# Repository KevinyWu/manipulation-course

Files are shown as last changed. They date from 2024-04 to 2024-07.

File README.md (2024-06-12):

# Robotic Manipulation Course

- [Robotic Manipulation Course](#robotic-manipulation-course)
  - [Course Setup](#course-setup)
  - [Dynamixel Robot Arm](#dynamixel-robot-arm)
    - [Required Materials](#required-materials)
    - [Assembly](#assembly)

## Course Setup

Clone the repo and create a virtual environment. We use Python 3.10.12.

```bash
# Clone the repository
git clone https://github.com/KevinyWu/manipulation-course.git
cd manipulation-course

# Create a virtual environment in the project root
python3 -m venv env

# Add the project to the PYTHONPATH in the virtual environment
echo 'export PYTHONPATH="$PYTHONPATH:/absolute/path/to/manipulation-course"' >> env/bin/activate

# Activate the virtual environment
source env/bin/activate

# Install the dependencies
pip install -r requirements.txt

# To deactivate the virtual environment
deactivate
```

## Dynamixel Robot Arm

This repository contains the files to build and control a low-cost robot arm that costs about $160. The design is adapted from [low_cost_robot](https://github.com/AlexanderKoch-Koch/low_cost_robot) by [Alexander Koch](https://github.com/AlexanderKoch-Koch).

This robot arm uses Dynamixel XL330 servo motors that weigh only 18g each. This makes the arm very lightweight and fast.
Dynamixel sells the U2D2 adapter to connect the servos to a computer. However, this is very expensive and the latency is very high. This build uses another cheaper adapter board instead.
The robot arm can be controlled with the Dynamixel SDK: ```pip install dynamixel-sdk```

### Required Materials

| Part | Cost | Buying link | Notes |
|---|---|---| --- |
| 5x Dynamixel XL330-M288 | $120  | https://www.robotis.us/dynamixel-xl330-m288-t/ | [Specs](https://emanual.robotis.com/docs/en/dxl/x/xl330-m288/)|
| XL330 Idler Wheel | $10  | https://www.robotis.us/fpx330-h101-4pcs-set/ | Pack of four; only three needed |
| XL330 Frame | $9 | https://www.robotis.us/fpx330-s101-4pcs-set/ | Pack of four; only one needed |
| Waveshare Serial Bus Servo Driver Board | $5  | https://www.waveshare.com/bus-servo-adapter-a.htm | |
| Waveshare OV5693 5MP USB Camera | $30  | https://www.waveshare.com/product/ov5693-5mp-usb-camera-a.htm | |
| 5V Power Supply | $6 | https://a.co/d/5u90NVp | |
| Table Clamp | $6 | https://a.co/d/4KEiYdV | |
| Wires | $7 | https://a.co/d/hQfk2cb | |
| Rubber Sheet | $2 | https://a.co/d/bEoalHQ | |
| USB-C Cable | $8 | https://a.co/d/fA40KHY | Pack of two, only one needed|
| Total | $194 | | |

There is usually a 10% discount code for the Robotis shop.

### Assembly

Video of the assembly: MAKE VIDEO

1. Print all parts with a 3D printer
   1. The STL files are in `hardware/stl`
   2. The parts are designed to be easy to print; only the moving part of the gripper needs supports
2. Scanning motors
   1. Connect the driver board to a computer (should work with Linux and MacOS)
   2. Figure out the device name (e.g. tty.usbmodem57380045631 for MacOS): ```ls /dev/tty.*```
   3. Scan each motor individually with [Dynamixel Wizard](https://emanual.robotis.com/docs/en/software/dynamixel/dynamixel_wizard2/)
      1. (Linux) Allow access to USB ports, then reboot for changes to take effect: `sudo usermod -aG dialout <your_account_id>; reboot`
      2. Set the baudrate to 1M for all motors
      3. Set the servo IDs to 1 for the shoulder to 5 for the gripper servo
3. Assembly
   1. Assemble the arm without the base
      1. Make sure that the servos are fixed in the same position as in the CAD
      2. Ensure the default servo angles are all 180 degrees (when the arm is in the position shown in the image below, all servos should be at 180 degrees as shown on the right image from Dynamixel Wizard)
   2. Screw the servo driver board onto the base
   3. Screw the base onto the arm
   4. Connect D, V, and G ports on the driver board to the shoulder rotation servo
   5. Connect successive servos to each other
   6. Connect the driver board to the power supply

<p align="center">
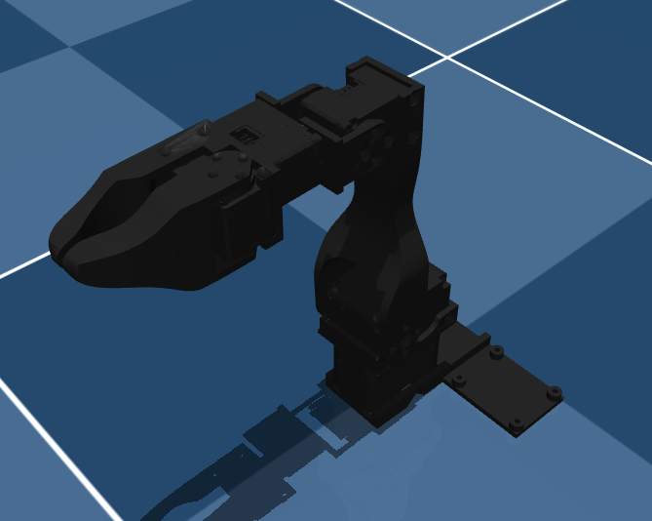
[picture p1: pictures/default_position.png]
default_position
   
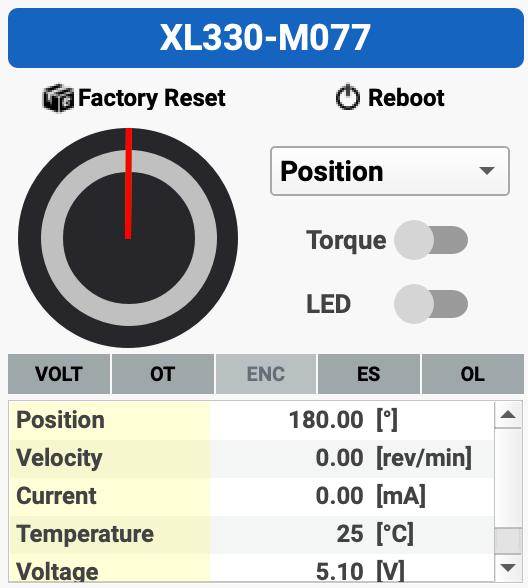
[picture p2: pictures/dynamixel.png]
dynamixel
   
</p>

**Note**: Ensure the default servo angles are all 180 degrees when the arm is in the position shown in the simulation above. Also note that counterclockwise is negative for rotation in Dynamixel Wizard.

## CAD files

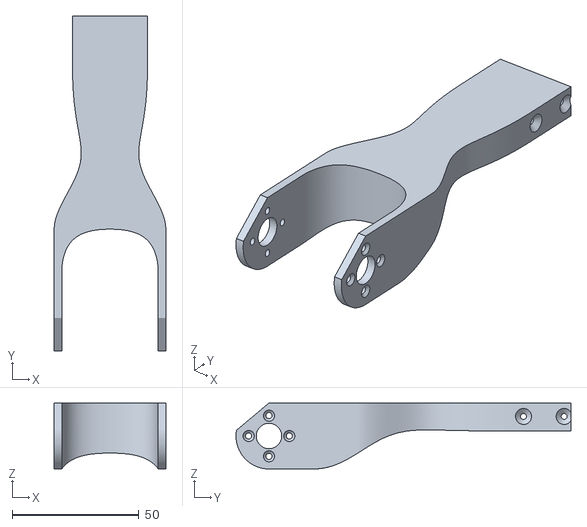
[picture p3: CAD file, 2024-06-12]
hardware/arm/shoulder_to_elbow.stl
44.0 x 132.0 x 26.0

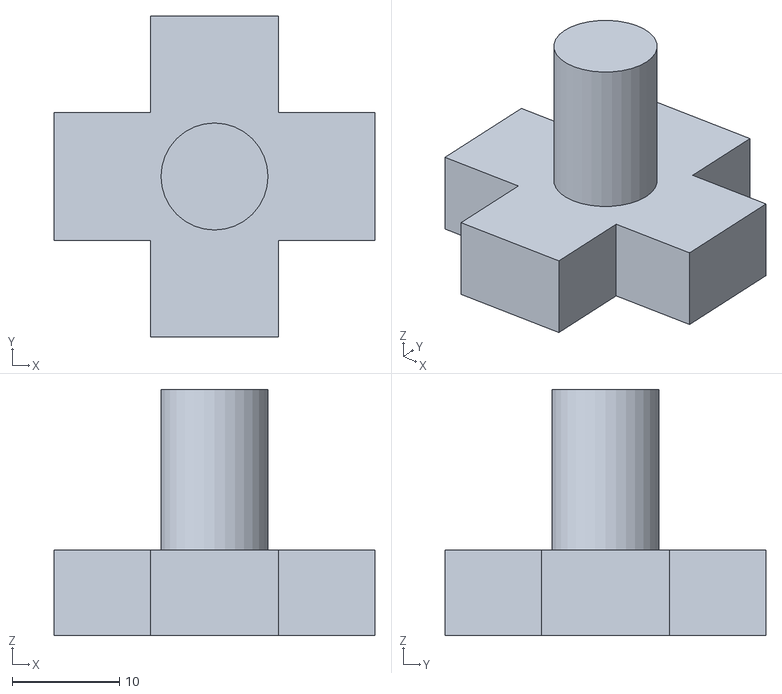
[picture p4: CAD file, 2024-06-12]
hardware/game/x.stl
30.0 x 30.0 x 23.0

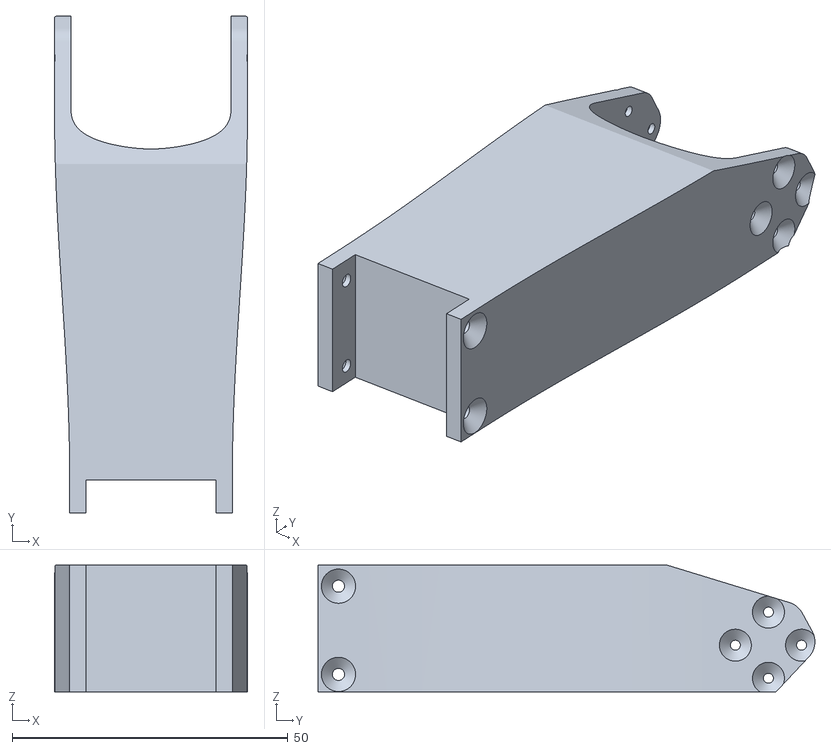
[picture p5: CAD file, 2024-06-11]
hardware/arm/elbow_to_wrist_extension.stl
35.0 x 90.1 x 23.0

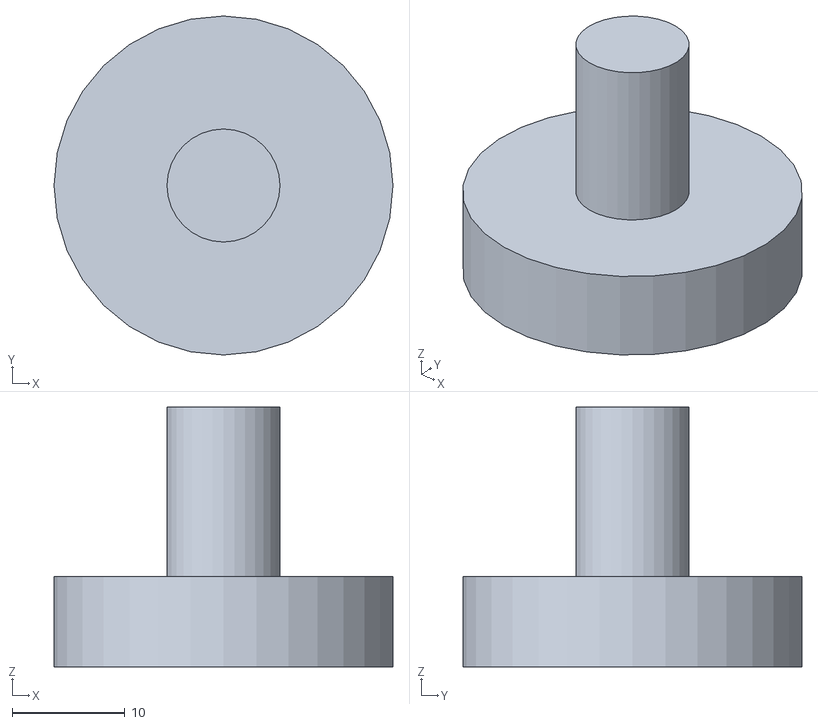
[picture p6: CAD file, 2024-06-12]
hardware/game/o.stl
30.0 x 30.0 x 23.0

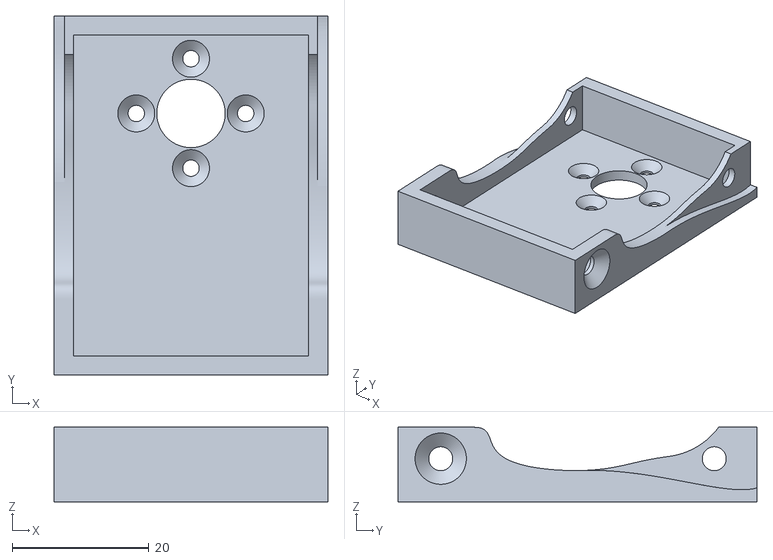
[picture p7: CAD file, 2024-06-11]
hardware/arm/shoulder_rotation.stl
40.0 x 52.5 x 10.9

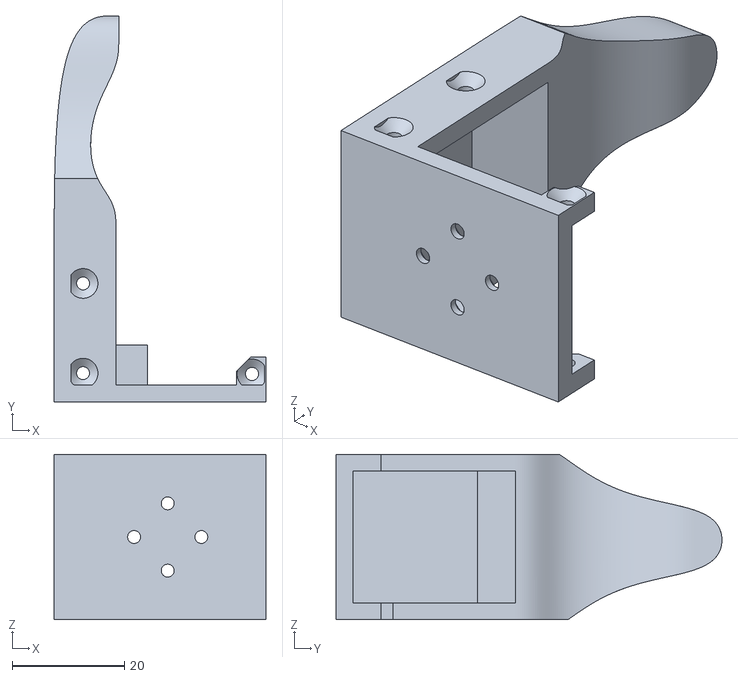
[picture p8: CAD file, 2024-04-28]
hardware/arm/gripper_static_part.stl
37.8 x 68.9 x 29.5

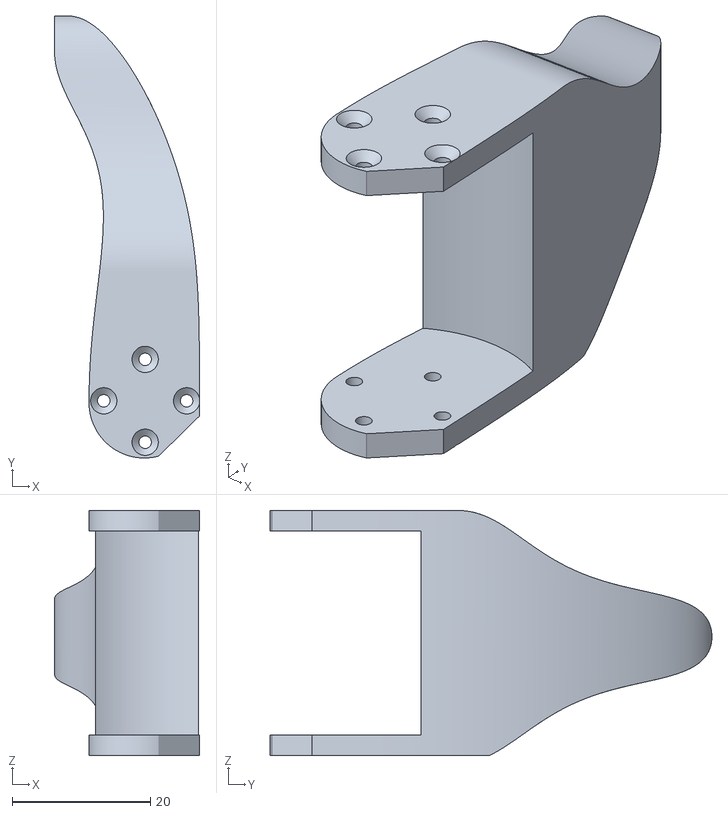
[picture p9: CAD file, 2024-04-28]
hardware/arm/gripper_moving_part.stl
21.0 x 64.0 x 35.5

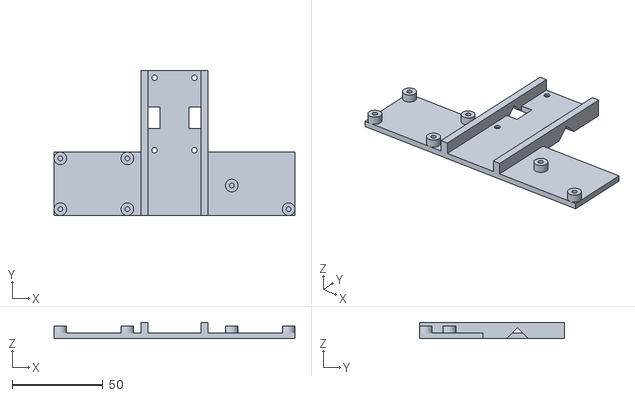
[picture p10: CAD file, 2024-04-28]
hardware/arm/base.stl
133.0 x 80.0 x 9.00

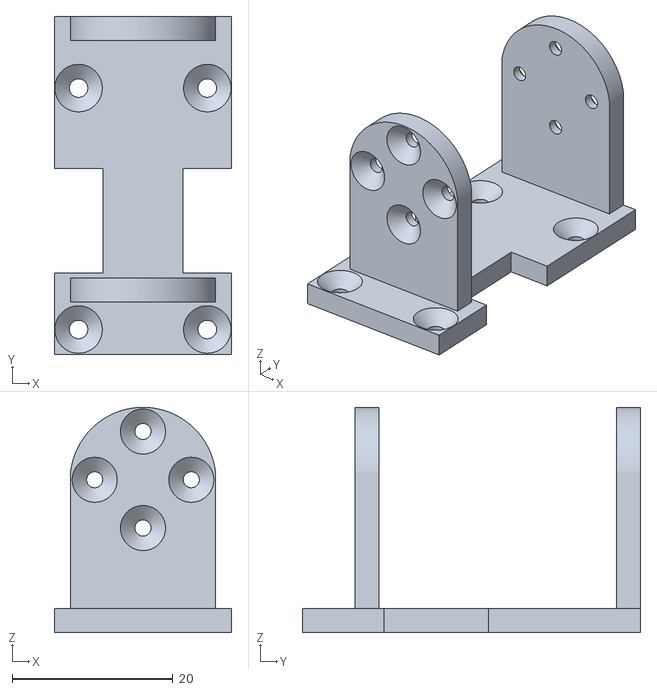
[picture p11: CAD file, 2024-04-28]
hardware/arm/elbow_to_wrist.stl
22.0 x 42.0 x 28.0

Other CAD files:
hardware/game/o.blend
hardware/game/x.blend

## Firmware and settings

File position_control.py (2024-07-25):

import json, time
import numpy as np
import pandas as pd
from robot.robot import Robot

CONVERSION_FACTOR = 4096 / 360

def load_robot_settings():
    with open('config.json') as f:
        config = json.load(f)
    arm_config = config['arm']
    return arm_config

def initialize_robot(arm_config):
    arm = Robot(device_name=arm_config['device_name'], 
                servo_ids=arm_config['servo_ids'],
                velocity_limit=arm_config['velocity_limit'],
                max_position_limit=arm_config['max_position_limit'],
                min_position_limit=arm_config['min_position_limit'],
                position_p_gain=arm_config['position_p_gain'],
                position_i_gain=arm_config['position_i_gain'])
    return arm

def change_servo_angle(arm, servo_id, delta):
    pos = arm.read_position()
    pos = [int(p) for p in pos]
    servo_id_index = arm.servo_ids.index(servo_id)
    pos[servo_id_index] += delta
    arm.set_and_wait_goal_pos(pos, servo_id=servo_id)
    # Print the current position of the servo after the move
    time.sleep(0.25)
    cur_pos = arm.read_position()
    positions_in_degrees = np.round(np.array(cur_pos) / CONVERSION_FACTOR, 2)
    df = pd.DataFrame({
        'ID': arm.servo_ids,
        'Degrees': positions_in_degrees
    })
    print('\n', df.to_string(index=False), '\n')

def main():
    arm_config = load_robot_settings()
    arm = initialize_robot(arm_config)
    
    # Go to home position
    arm.set_and_wait_goal_pos(arm_config['home_pos'])

    # Position control loop
    print('\n\nWelcome to position control mode!')
    print('Enter servo ID and delta angle (in degrees) to move the servo.')
    print('Delta angle can be positive or negative, and the servo angle will change by that amount.')
    print('The current position of the servo will be printed after each move.')
    print('Enter "q" at any time to quit.\n\n')
    while True:
        try:
            user_input = input('Enter servo ID: ')
            if user_input.lower() == 'q':
                break
            servo_id = int(user_input)
            if servo_id not in arm_config['servo_ids']:
                print(f'Invalid servo ID. Please enter one of {arm_config["servo_ids"]}\n')
                continue
            delta_input = input('Enter delta angle: ')
            if delta_input.lower() == 'q':
                break
            delta = float(delta_input)
            delta = int(delta * CONVERSION_FACTOR)
            change_servo_angle(arm, servo_id, delta)
        except KeyboardInterrupt:
            break

    # Go to rest position and disable torque
    arm.set_and_wait_goal_pos(arm_config['rest_pos'])
    arm._disable_torque()

if __name__ == '__main__':
    main()

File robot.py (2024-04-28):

import numpy as np
from dynamixel import OperatingMode, ReadAttribute
import time, json
from dynamixel_sdk import GroupSyncRead, GroupSyncWrite, DXL_LOBYTE, DXL_HIBYTE, DXL_LOWORD, DXL_HIWORD
from enum import Enum, auto
from typing import Union


class MotorControlType(Enum):
    PWM = auto()
    POSITION_CONTROL = auto()
    DISABLED = auto()
    UNKNOWN = auto()


class Robot:
    def __init__(self, dynamixel, baudrate=1_000_000, servo_ids=[1, 2, 3, 4, 5]):
        self.servo_ids = servo_ids
        self.dynamixel = dynamixel
        self.position_reader = GroupSyncRead(
            self.dynamixel.portHandler,
            self.dynamixel.packetHandler,
            ReadAttribute.POSITION.value,
            4)
        for id in self.servo_ids:
            self.position_reader.addParam(id)

        self.velocity_reader = GroupSyncRead(
            self.dynamixel.portHandler,
            self.dynamixel.packetHandler,
            ReadAttribute.VELOCITY.value,
            4)
        for id in self.servo_ids:
            self.velocity_reader.addParam(id)

        self.pos_writer = GroupSyncWrite(
            self.dynamixel.portHandler,
            self.dynamixel.packetHandler,
            self.dynamixel.ADDR_GOAL_POSITION,
            4)
        for id in self.servo_ids:
            self.pos_writer.addParam(id, [2048])

        self.pwm_writer = GroupSyncWrite(
            self.dynamixel.portHandler,
            self.dynamixel.packetHandler,
            self.dynamixel.ADDR_GOAL_PWM,
            2)
        for id in self.servo_ids:
            self.pwm_writer.addParam(id, [2048])
        self._disable_torque()
        self.motor_control_state = MotorControlType.DISABLED

    def read_position(self, tries=2):
        """
        Reads the joint positions of the robot. 2048 is the center position. 0 and 4096 are 180 degrees in each direction.
        :param tries: maximum number of tries to read the position
        :return: list of joint positions in range [0, 4096]
        """
        result = self.position_reader.txRxPacket()
        if result != 0:
            if tries > 0:
                return self.read_position(tries=tries - 1)
            else:
                print(f'failed to read position!!!!!!!!!!!!!!!!!!!!!!!!!!!!!')
        positions = []
        for id in self.servo_ids:
            position = self.position_reader.getData(id, ReadAttribute.POSITION.value, 4)
            if position > 2 ** 31:
                position -= 2 ** 32
            positions.append(position)
        return positions

    def read_velocity(self):
        """
        Reads the joint velocities of the robot.
        :return: list of joint velocities,
        """
        self.velocity_reader.txRxPacket()
        velocties = []
        for id in self.servo_ids:
            velocity = self.velocity_reader.getData(id, ReadAttribute.VELOCITY.value, 4)
            if velocity > 2 ** 31:
                velocity -= 2 ** 32
            velocties.append(velocity)
        return velocties

    def set_goal_pos(self, action):
        """
        :param action: list or numpy array of target joint positions in range [0, 4096]
        """
        if not self.motor_control_state is MotorControlType.POSITION_CONTROL:
            self._set_position_control()
        for i, motor_id in enumerate(self.servo_ids):
            data_write = [DXL_LOBYTE(DXL_LOWORD(action[i])),
                          DXL_HIBYTE(DXL_LOWORD(action[i])),
                          DXL_LOBYTE(DXL_HIWORD(action[i])),
                          DXL_HIBYTE(DXL_HIWORD(action[i]))]
            self.pos_writer.changeParam(motor_id, data_write)

        self.pos_writer.txPacket()

    def set_pwm(self, action):
        """
        Sets the pwm values for the servos.
        :param action: list or numpy array of pwm values in range [0, 885]
        """
        if not self.motor_control_state is MotorControlType.PWM:
            self._set_pwm_control()
        for i, motor_id in enumerate(self.servo_ids):
            data_write = [DXL_LOBYTE(DXL_LOWORD(action[i])),
                          DXL_HIBYTE(DXL_LOWORD(action[i])),
                          ]
            self.pwm_writer.changeParam(motor_id, data_write)

        self.pwm_writer.txPacket()

    def set_trigger_torque(self):
        """
        Sets a constant torque torque for the last servo in the chain. This is useful for the trigger of the leader arm
        """
        self.dynamixel._enable_torque(self.servo_ids[-1])
        self.dynamixel.set_pwm_value(self.servo_ids[-1], 200)

    def limit_pwm(self, limit: Union[int, list, np.ndarray]):
        """
        Limits the pwm values for the servos in for position control
        @param limit: 0 ~ 885
        @return:
        """
        if isinstance(limit, int):
            limits = [limit, ] * 5
        else:
            limits = limit
        self._disable_torque()
        for motor_id, limit in zip(self.servo_ids, limits):
            self.dynamixel.set_pwm_limit(motor_id, limit)
        self._enable_torque()

    def _disable_torque(self):
        print(f'disabling torque for servos {self.servo_ids}')
        for motor_id in self.servo_ids:
            self.dynamixel._disable_torque(motor_id)

    def _enable_torque(self):
        print(f'enabling torque for servos {self.servo_ids}')
        for motor_id in self.servo_ids:
            self.dynamixel._enable_torque(motor_id)

    def _set_pwm_control(self):
        self._disable_torque()
        for motor_id in self.servo_ids:
            self.dynamixel.set_operating_mode(motor_id, OperatingMode.PWM)
        self._enable_torque()
        self.motor_control_state = MotorControlType.PWM

    def _set_position_control(self):
        self._disable_torque()
        for motor_id in self.servo_ids:
            self.dynamixel.set_operating_mode(motor_id, OperatingMode.POSITION)
        self._enable_torque()
        self.motor_control_state = MotorControlType.POSITION_CONTROL

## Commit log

2024-06-11 more parts
    [base.stl, big_base.stl, elbow_to_wrist_extension.stl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]
2024-06-12 tic tac toe
    [o.blend, o.stl, x.stl]
2024-06-18 game board
    [o.blend, o.stl, x.blend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]
